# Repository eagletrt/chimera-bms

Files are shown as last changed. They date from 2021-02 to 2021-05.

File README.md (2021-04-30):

# Chimera high voltage BMS  - hardware

## Libraries
The projects don't include the libraries since they use the KiCAD official ones.
Set accordingly the variables `${KICAD_SYMBOL_DIR}` and `${KISYSMOD}` for 
`kicad-symbols` and `kicad-footprints` respectively.
**For `kicad-symbols` checkout the repo to `v5` for now to have the legacy ones.**

Don't rescue symbols!

## Repo structure
```
chimera-bms:hw-master
|-- docs/       # Docs and datasheets of common interest
|-- mainboard/  # MainBoard hardware project folder
|-- cellboard/  # CellBoard hardware project folder
```

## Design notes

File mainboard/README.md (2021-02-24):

# MAIN BOARD
Formula SAE - unitn

## Authors
Latest first:
- Filippo Volpe
- Gregor Gombac
- Jesus probably

## Project structure
```
mainboard
|-- MainBoard.pro           # Project file
|-- MainBoard.sch           # Schematic root
|-- MainBoard.kicad_pcb     # Board layout file
|-- MainBoard-cache.lib     # Local cache of symbols
|-- fp-info-cache           # Cache of footprints
|-- fp-lib-table            # List of footprint lib files
|-- sym-lib-table           # List of symbols lib files
|-- lib_sch/                # Local symbol library files
|-- modules/                # Local symbol library files
|   |-- MainBoard.pretty/   # Local footprint library files
|   |-- packages3d/         # 3D models
|-- outputs/
|   |-- MainBoard.stp       # Board 3D step file
|   |-- images/             # Board renders and such
|   |-- gerber/             # Gerbers outputs
|   |-- netlists/           # Netlists outputs
|-- docs/                   # Additional related documents and outputs
|   |-- Decoupling.txt      # List of decoupling capacitor needed
|   |-- bom/                # BOM folder
```

## Notes
The board file is from V2, it has not been updated

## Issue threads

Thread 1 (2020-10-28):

Add handcart sensing

Bonnee, 2020-10-28:
Automatically reconfigure the CAN-bus and initiate charging procedure when connected to the handcart.

volpx, 2021-02-28:
The pin for handcart detection has been added, the hardware side of the issue can be closed

Bonnee, 2021-02-28:
Perfect! How is the pin configured (pull-up or down)? Ideally it should be identical to the new Mainboard's one.

volpx, 2021-02-28:
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

volpx, 2021-02-28:
But it's not on the main connector as in fenice. the pinout is incompatible anyway.

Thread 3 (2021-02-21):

Add pin for hand cart detection

Bonnee, 2021-02-21:
Add input pin to check whether the battery is plugged into the car or is on the charging hand cart

Bonnee, 2021-02-21:
Duplicate of #1

Closed 2021-02-21.

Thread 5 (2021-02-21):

ADC doesn't work

Bonnee, 2021-02-21:
The external ADC of the old design doesn't work. I think it's better to replace it with the new Mainboard's design which seems to work.

volpx, 2021-02-24:
Old isoADC: LTC1865L
New from fenice: Si8900

volpx, 2021-02-27:
I'm working on changing the ADC but the Si8900 needs a UART+one output GPIO. So I moved some pins around to use empty pins and now the pinout is full:
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

volpx, 2021-02-27:
If we will need a MCU upgrade this would be a good time to.

Bonnee, 2021-02-27:
Wold going for the same MCU in a bigger package make sense? We don't really need more compute power or peripherals on this board.

volpx, 2021-02-28:
GG just wrote me suggesting to use the I2C version. Do we have one in the lab to try?

Bonnee, 2021-02-28:
We can do with the I2C version. I don't know if we have any of those chips in lab, but I don't think so.
What kind of memories do we have on the bus?

volpx, 2021-02-28:
two m24m02

Bonnee, 2021-02-28:
Never knew of their existance lol. You can remove one of those.

volpx, 2021-02-28:
Not a problem if they are there, we can just not populate the footprint. We go for the I2C adc then and call the issue closed once i push.

Closed 2021-02-28.

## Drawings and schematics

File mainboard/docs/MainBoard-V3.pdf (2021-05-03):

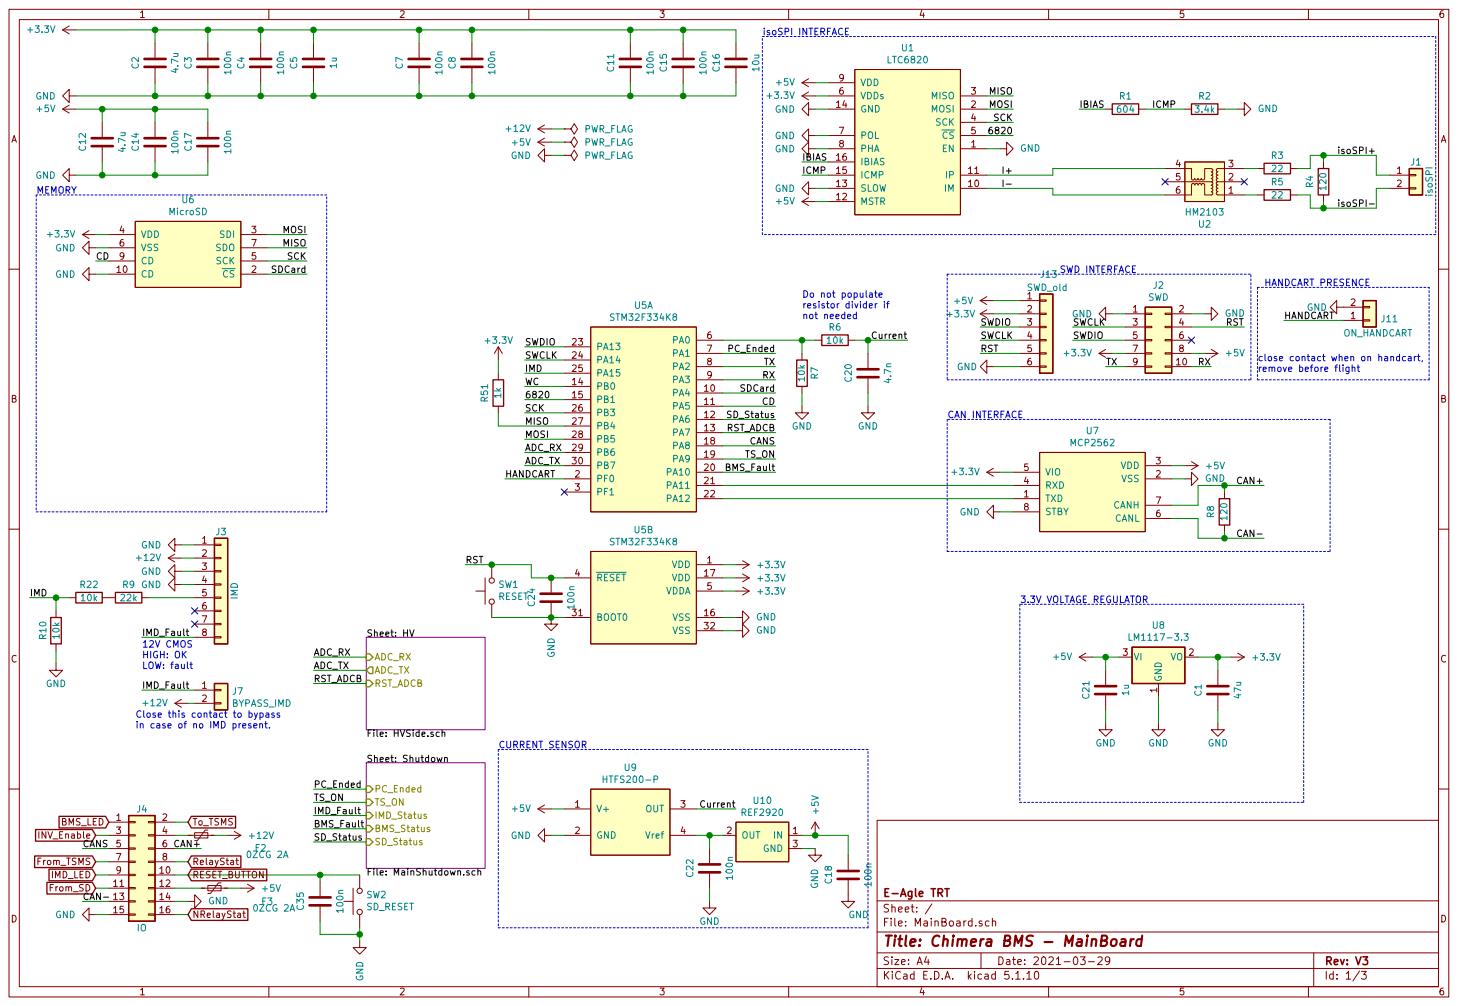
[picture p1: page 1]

close contact when on handcart, remove before flight HANDCART PRESENCE CAN INTERFACE Close this contact to bypass

resistor divider if not needed CURRENT SENSOR

in case of no IMD present.

Sheet: Shutdown File: MainShutdown.sch PC_Ended TS_ON

File: MainBoard.sch Sheet: / E-Agle TRT

GND
Id: 1/3 Title: Chimera BMS - MainBoard

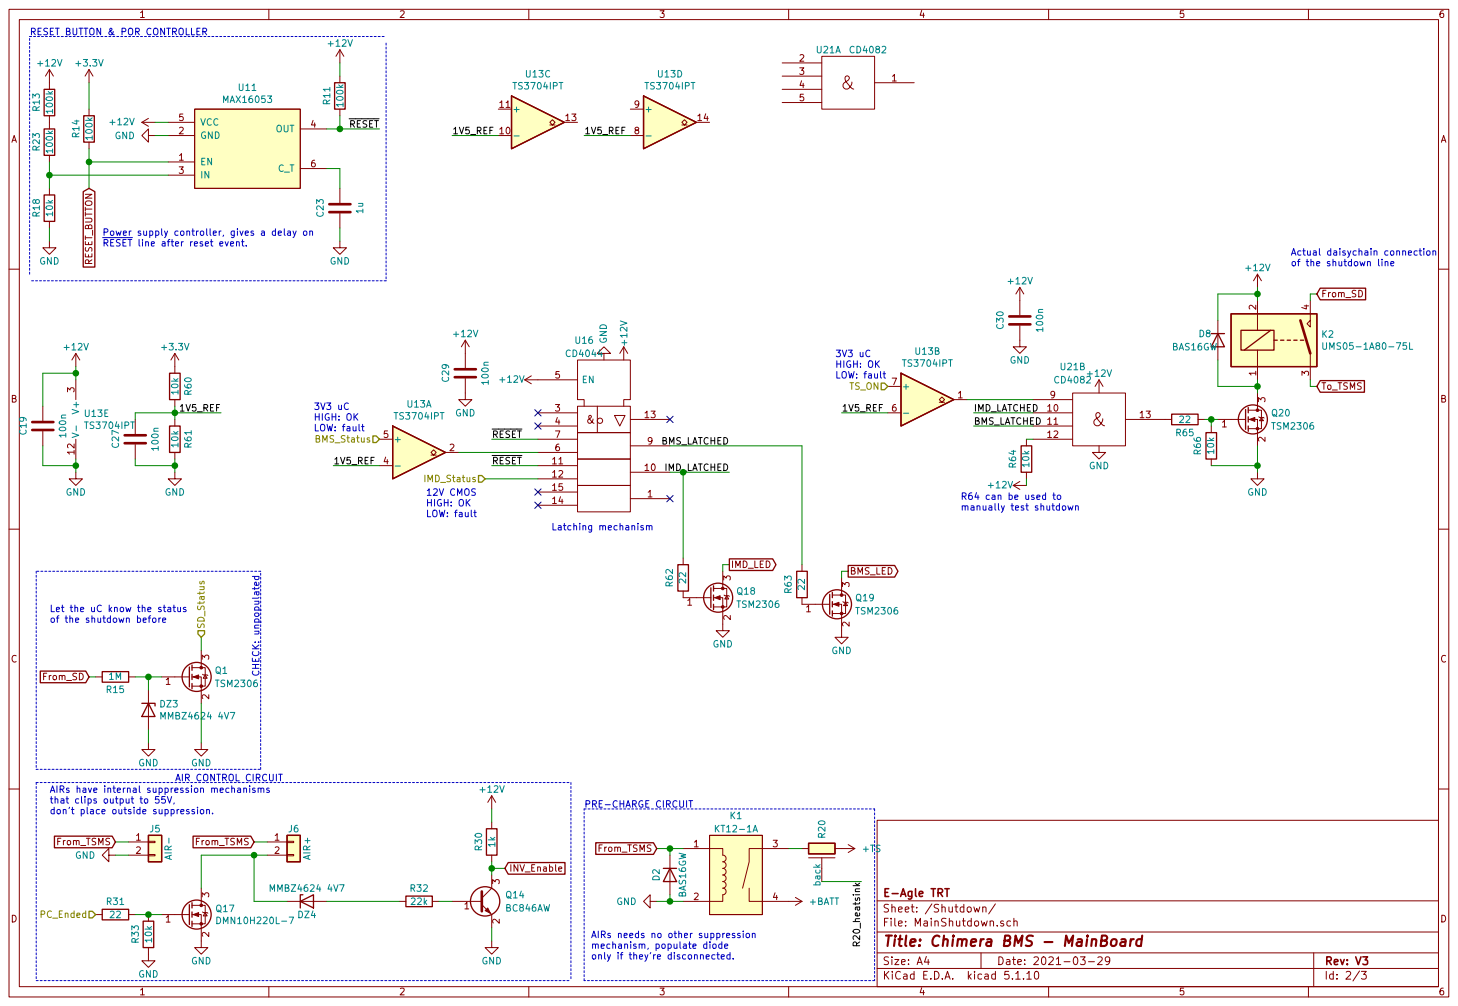
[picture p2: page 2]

RESET BUTTON & POR CONTROLLER

LOW: fault Power supply controller, gives a delay on RESET line after reset event. AIRs have internal suppression mechanisms

Actual daisychain connection of the shutdown line PRE-CHARGE CIRCUIT AIR CONTROL CIRCUIT
+12V GND

3 4 K2UMS05-1A80-75L GND
LOW: fault CHECK: unpopulated

Let the uC know the status of the shutdown before

R64 can be used to manually test shutdown

that clips output to 55V,
don't place outside suppression.

File: MainShutdown.sch Sheet: /Shutdown/ E-Agle TRT

Id: 2/3 Title: Chimera BMS - MainBoard

AIRs needs no other suppression
mechanism, populate diode
only if they're disconnected.

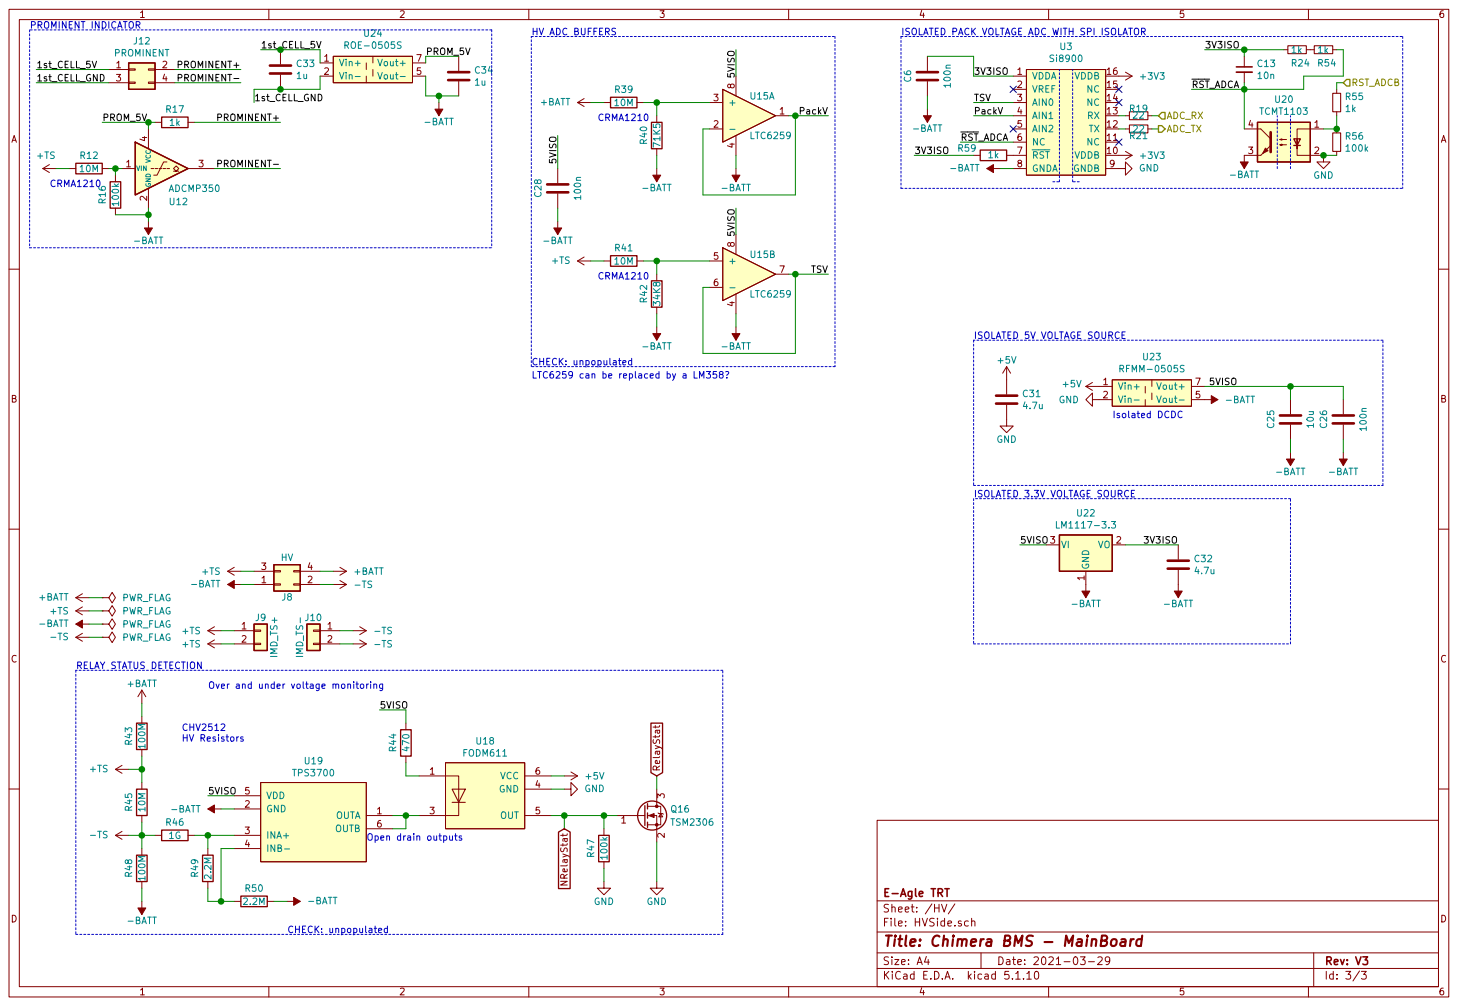
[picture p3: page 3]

ISOLATED PACK VOLTAGE ADC WITH SPI ISOLATOR

ISOLATED 5V VOLTAGE SOURCE CHECK: unpopulated

LTC6259 can be replaced by a LM358?

CHECK: unpopulated CHV2512 HV Resistors RELAY STATUS DETECTION Over and under voltage monitoring

Id: 3/3 Title: Chimera BMS - MainBoard

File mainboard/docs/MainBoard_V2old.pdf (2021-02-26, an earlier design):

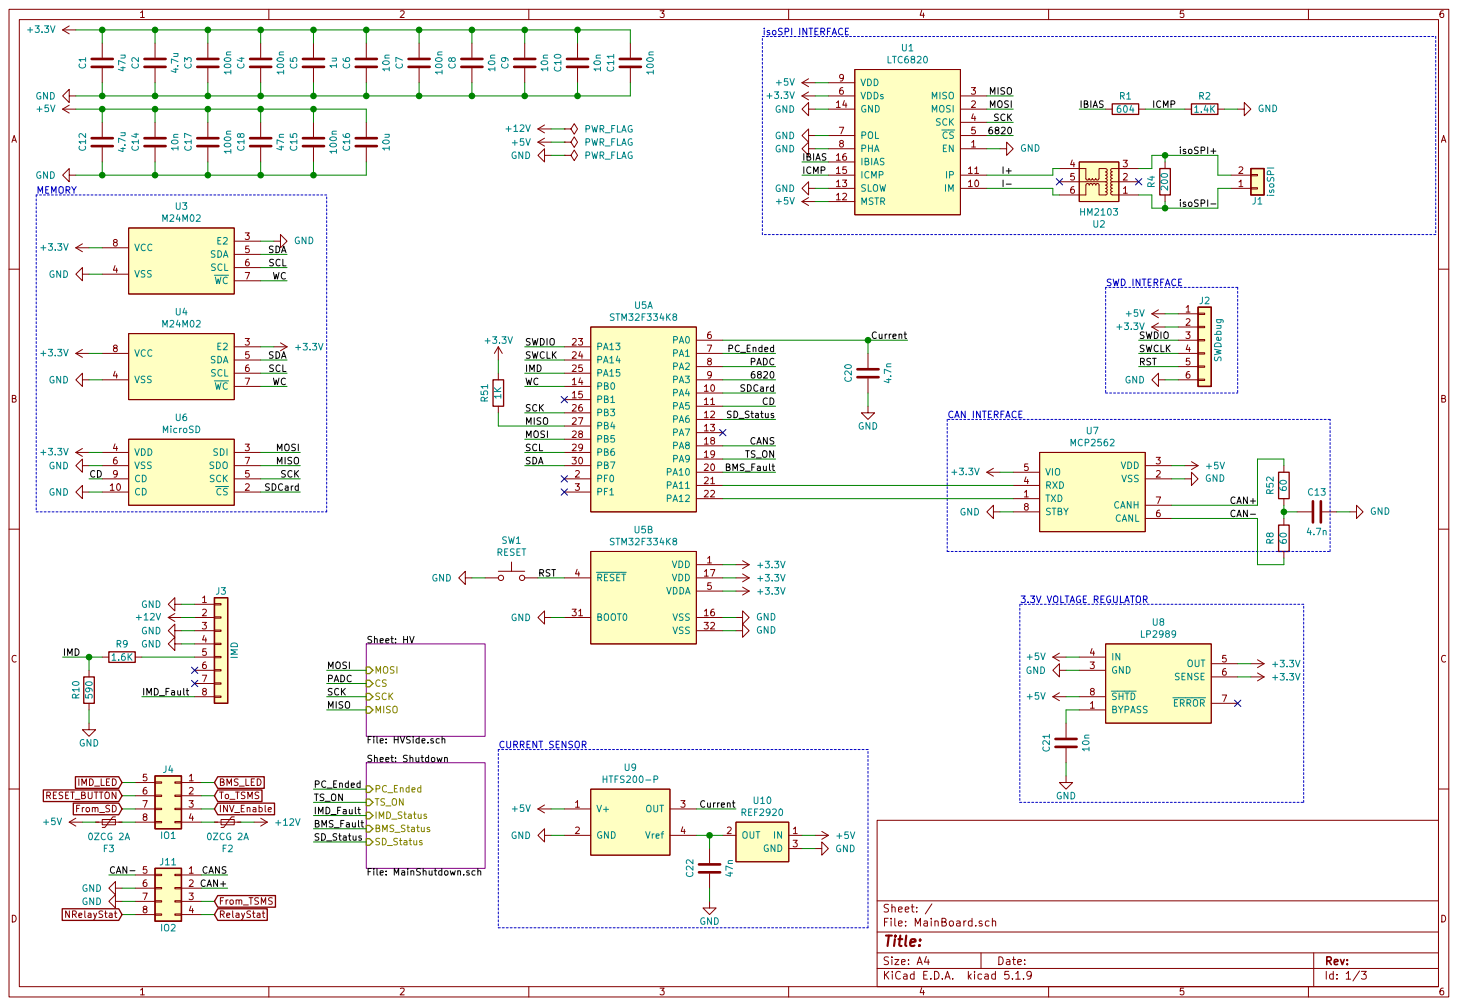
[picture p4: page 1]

SWD INTERFACE CURRENT SENSOR

File: HVSide.sch MOSI CS

Id: 1/3 Title: File: MainBoard.sch Sheet: / Sheet: Shutdown File: MainShutdown.sch PC_Ended TS_ON

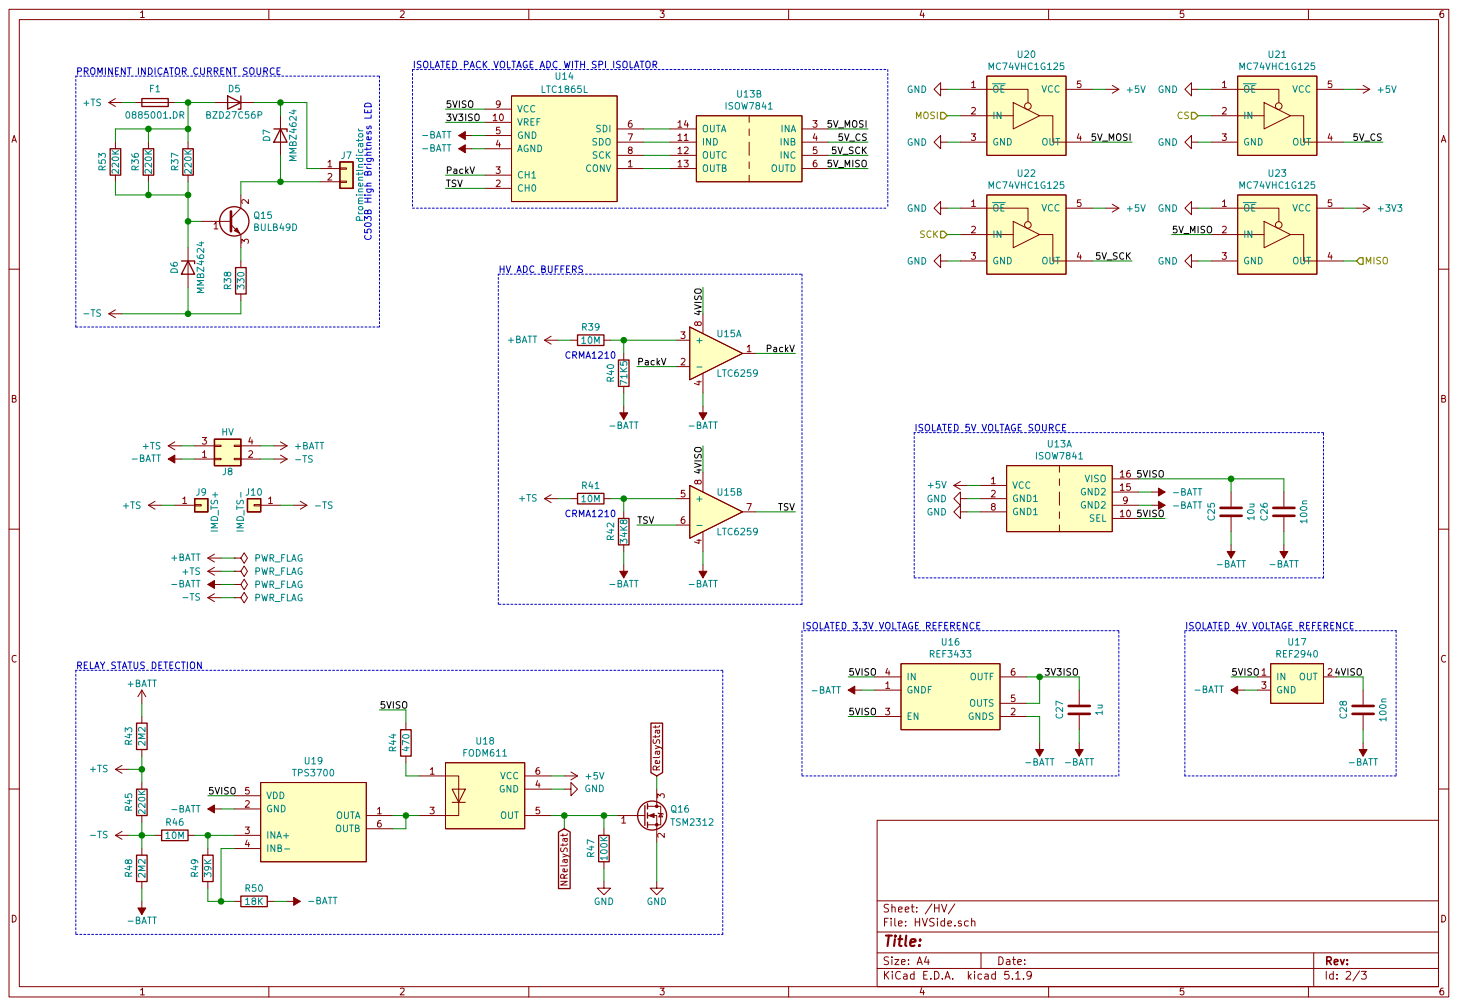
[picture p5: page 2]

ISOLATED PACK VOLTAGE ADC WITH SPI ISOLATOR

Id: 2/3 Title: File: HVSide.sch Sheet: /HV/

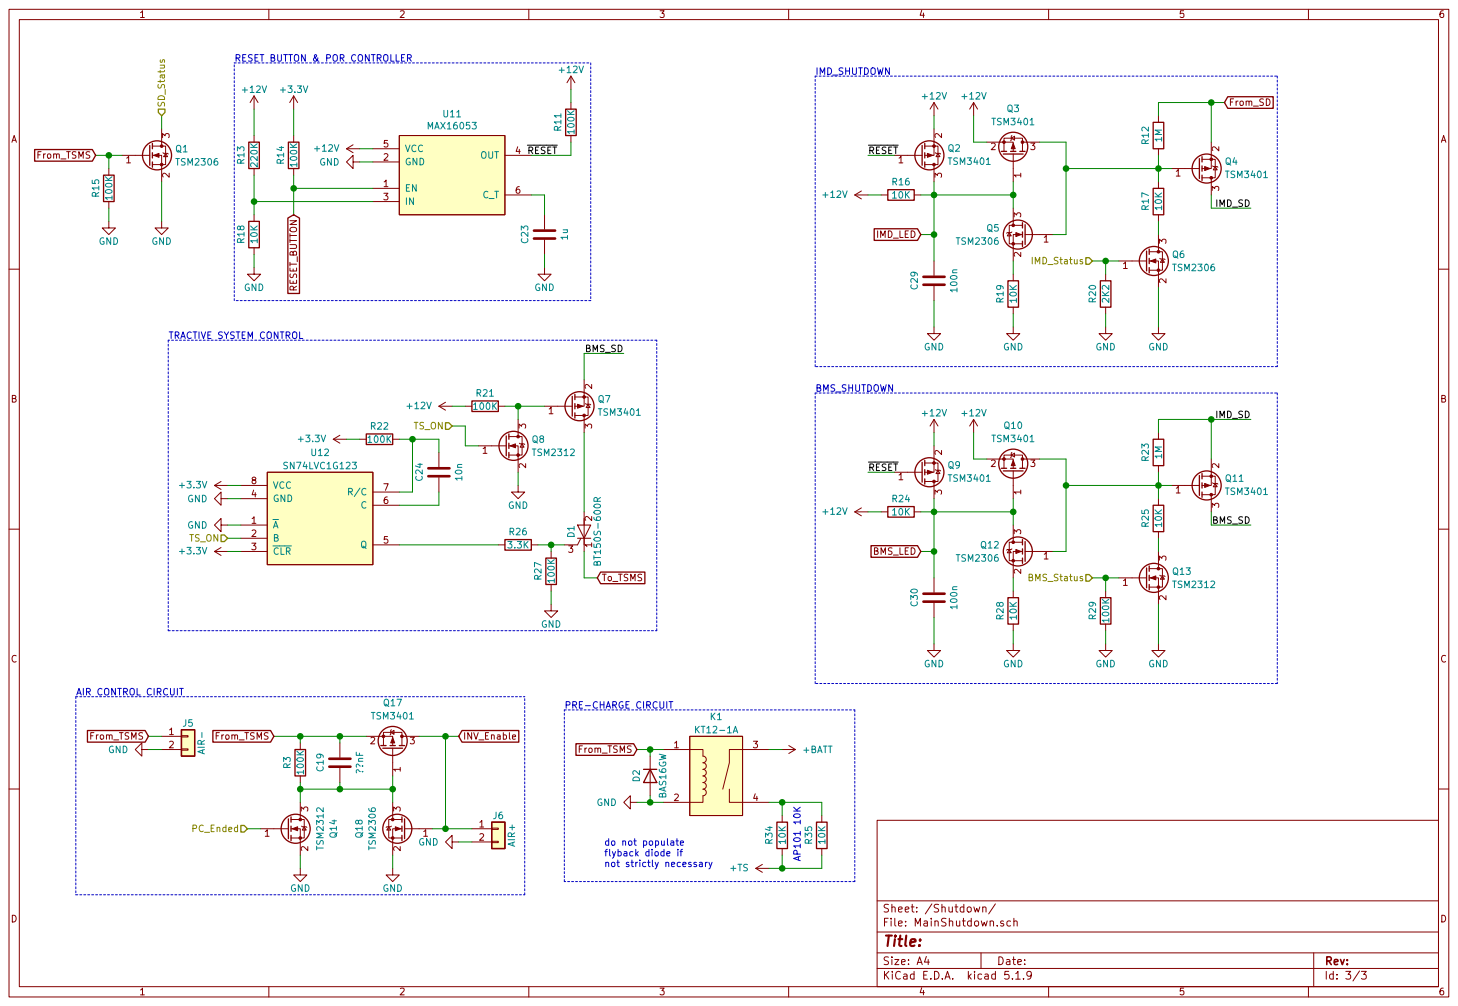
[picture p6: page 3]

TRACTIVE SYSTEM CONTROL RESET BUTTON & POR CONTROLLER

PRE-CHARGE CIRCUIT AIR CONTROL CIRCUIT

Id: 3/3 Title: File: MainShutdown.sch Sheet: /Shutdown/ +BATT

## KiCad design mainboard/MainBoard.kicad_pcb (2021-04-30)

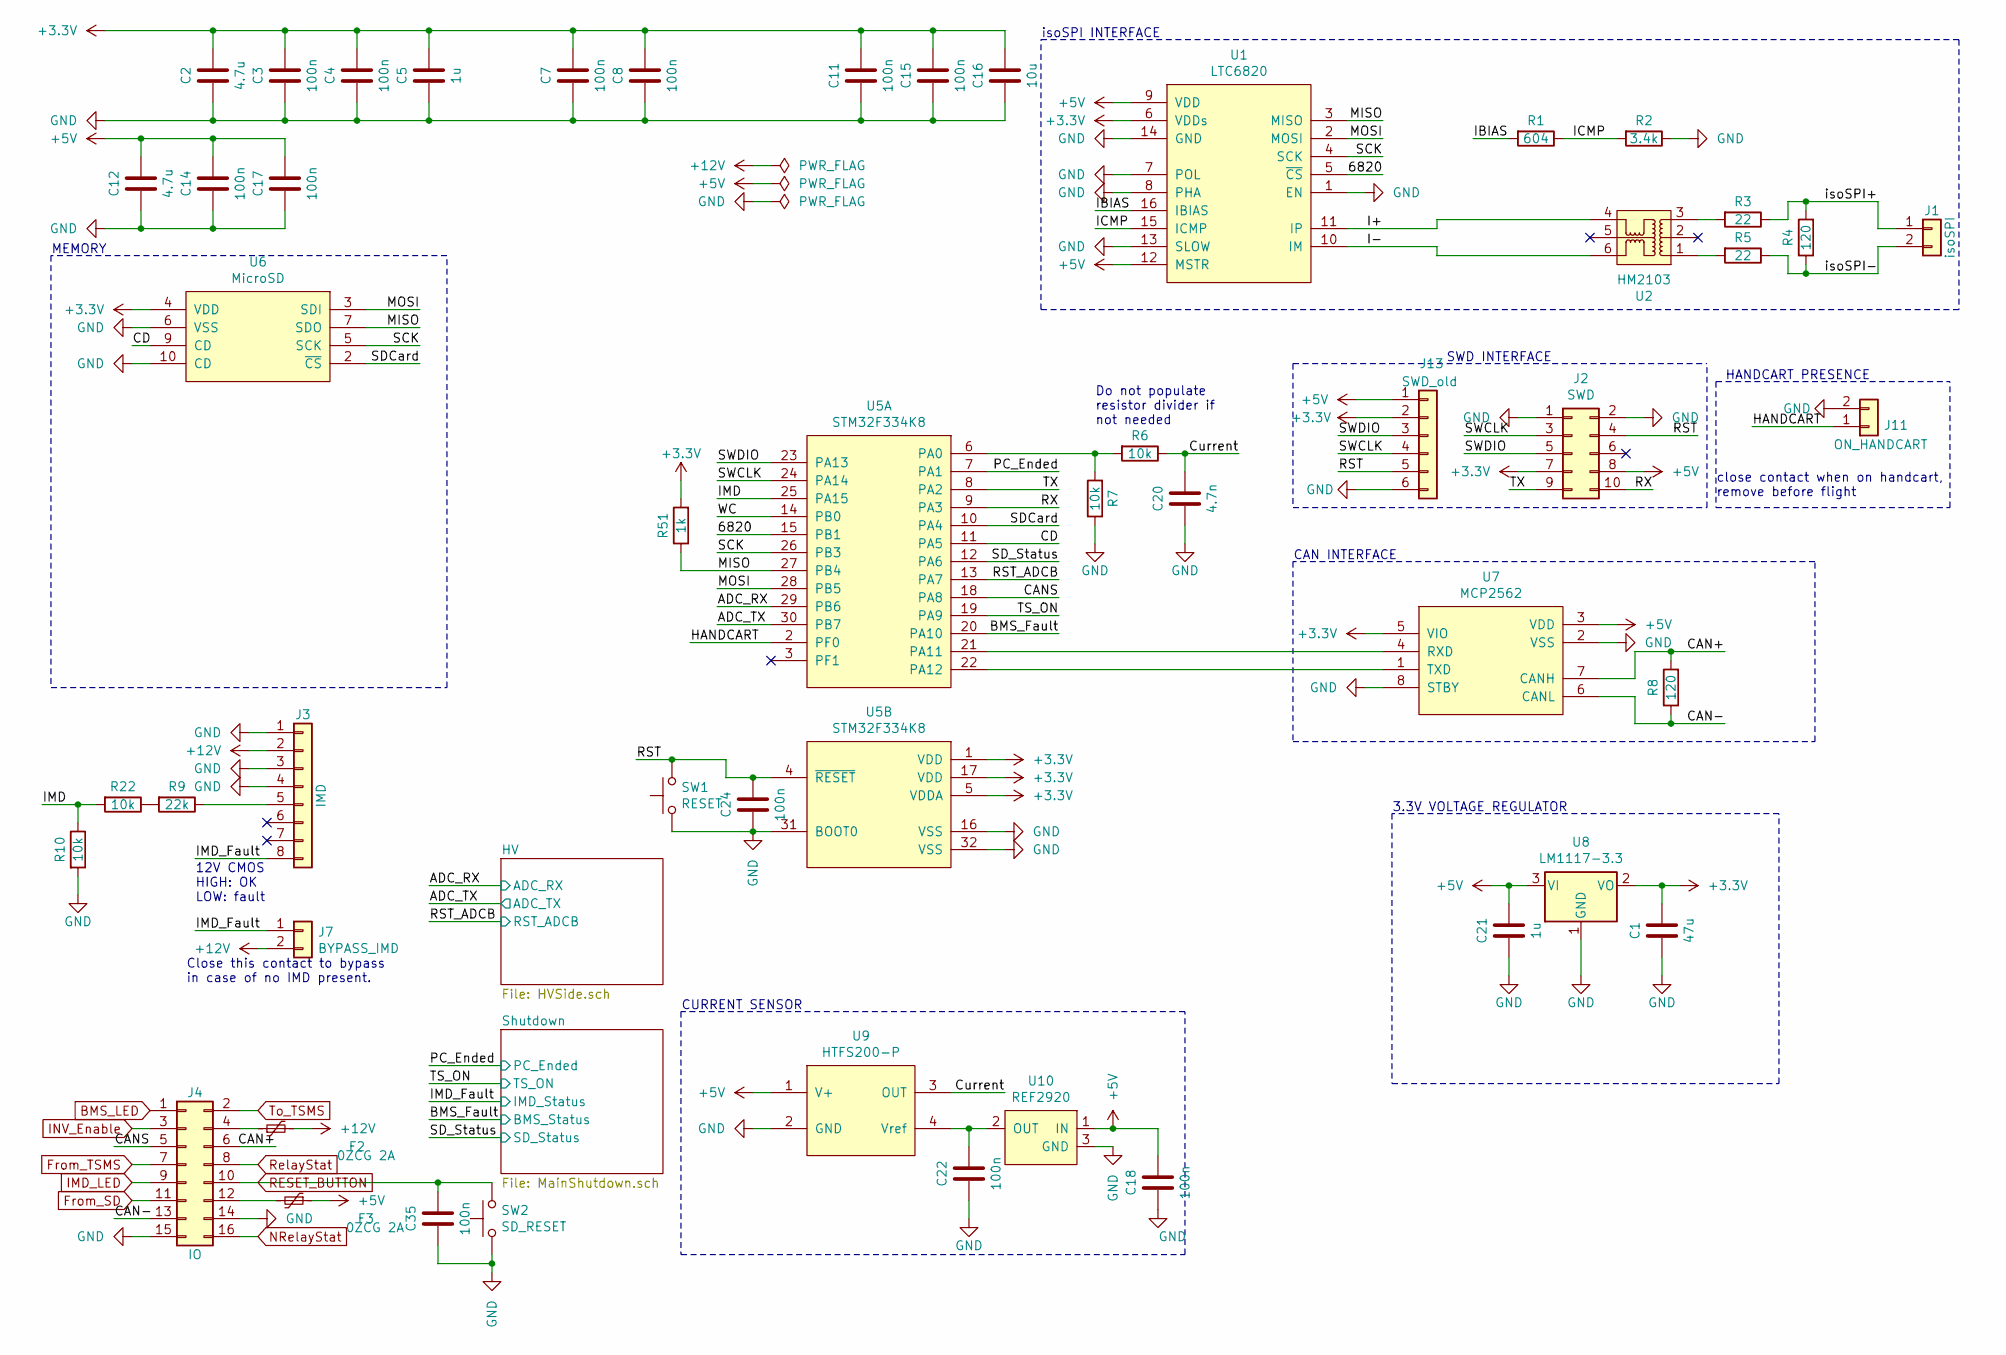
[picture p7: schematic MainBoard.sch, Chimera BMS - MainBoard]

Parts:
C1: 47u; C_1206_3216Metric
C2, C12: 4.7u; C_0805_2012Metric
C3, C4, C7, C8, C11, C14, C15, C17, C18, C22, C24, C35: 100n; C_0603_1608Metric
C5, C21: 1u; C_0805_2012Metric
C16: 10u; C_0805_2012Metric
C20: 4.7n; C_0603_1608Metric
F2, F3: 0ZCG 2A; Fuse_1812_4532Metric
J1: isoSPI; Molex_Micro-Fit_3.0_43650-0215_1x02_P3.00mm_Vertical
J2: SWD; PinHeader_2x05_P2.54mm_Vertical
J3: IMD; PinHeader_1x08_P3mm_Vertical
J4: IO; Molex_Micro-Fit_3.0_43045-1612_2x08_P3.00mm_Vertical
J7: BYPASS_IMD; PinHeader_1x02_P2.54mm_Vertical
J11: ON_HANDCART; PinHeader_1x02_P2.54mm_Vertical
J13: SWD_old; PinHeader_1x06_P2.54mm_Vertical
R1: 604; R_0805_2012Metric
R2: 3.4k; R_0805_2012Metric
R3, R5: 22; R_0805_2012Metric
R4, R8: 120; R_0805_2012Metric
R6, R7, R10, R22: 10k; R_0805_2012Metric
R9: 22k; R_0805_2012Metric
R51: 1k; R_0805_2012Metric
SW1: RESET; SW_SPST_FSMSM
SW2: SD_RESET; SW_SPST_FSMSM
U1: LTC6820; MSOP-16
U2: HM2103
U5: STM32F334K8; LQFP-32_7x7mm_P0.8mm
U6: MicroSD; Molex_MicroSD_PushPull
U7: MCP2562; SOIC-8_3.9x4.9mm_P1.27mm
U8: LM1117-3.3; SOT-223-3_TabPin2
U9: HTFS200-P; HTFS 200-P
U10: REF2920; SOT-23

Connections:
+5V: C12.1, C14.1, C17.1, C18.1, C21.1, F3.1, J2.8, J13.1, U1.9 (VDD), U1.12 (MSTR), U7.3 (VDD), U8.3 (VI), U9.1 (V+), U10.1 (IN); also elsewhere on the board
+12V: F2.2, J3.2, J7.2; also elsewhere on the board
/6820: U1.5 (~CS), U5.15 (PB1)
/ADC_RX: U5.29 (PB6); also elsewhere on the board
/ADC_TX: U5.30 (PB7); also elsewhere on the board
/BMS_Fault: U5.20 (PA10); also elsewhere on the board
/CAN+: J4.6, R8.2, U7.7 (CANH)
/CAN-: J4.13, R8.1, U7.6 (CANL)
/CANS: J4.5, U5.18 (PA8)
/CD: U5.11 (PA5), U6.9 (CD)
/Current: C20.1, R6.1, U9.3 (OUT)
/HANDCART: J11.1, U5.2 (PF0)
/I+: U1.11 (IP), U2.4
/I-: U1.10 (IM), U2.6
/IBIAS: R1.2, U1.16 (IBIAS)
/ICMP: R1.1, R2.2, U1.15 (ICMP)
/IMD: R10.1, R22.2, U5.25 (PA15)
/IMD_Fault: J3.8, J7.1; also elsewhere on the board
/MISO: R51.1, U1.3 (MISO), U5.27 (PB4), U6.7 (SDO)
/MOSI: U1.2 (MOSI), U5.28 (PB5), U6.3 (SDI)
/PC_Ended: U5.7 (PA1); also elsewhere on the board
/RST: C24.1, J2.4, J13.5, SW1.2, U5.4 (~RESET)
/RST_ADCB: U5.13 (PA7); also elsewhere on the board
/RX: J2.10, U5.9 (PA3)
/SCK: U1.4 (SCK), U5.26 (PB3), U6.5 (SCK)
/SDCard: U5.10 (PA4), U6.2 (~CS)
/SD_Status: U5.12 (PA6); also elsewhere on the board
/SWCLK: J2.3, J13.4, U5.24 (PA14)
/SWDIO: J2.5, J13.3, U5.23 (PA13)
/TS_ON: U5.19 (PA9); also elsewhere on the board
/TX: J2.9, U5.8 (PA2)
/WC: U5.14 (PB0)
/isoSPI+: J1.1, R3.1, R4.2
/isoSPI-: J1.2, R4.1, R5.1
BMS_LED: J4.1; also elsewhere on the board
From_SD: J4.11; also elsewhere on the board
From_TSMS: J4.7; also elsewhere on the board
GND: C1.2, C2.2, C3.2, C4.2, C5.2, C7.2, C8.2, C11.2, C12.2, C14.2, C15.2, C16.2, C17.2, C18.2, C20.2, C21.2, C22.2, C24.2, C35.2, J2.1, J2.2, J3.1, J3.3, J3.4, J4.14, J4.15, J11.2, J13.6, R2.1, R7.1, R10.2, SW1.1, SW2.1, U1.1 (EN), U1.7 (POL), U1.8 (PHA), U1.13 (SLOW), U1.14 (GND), U5.16 (VSS), U5.31 (BOOT0), U5.32 (VSS), U6.6 (VSS), U6.10 (CD), U7.2 (VSS), U7.8 (STBY), U8.1 (GND), U9.2 (GND), U10.3 (GND); also elsewhere on the board
IMD_LED: J4.9; also elsewhere on the board
INV_Enable: J4.3; also elsewhere on the board
NRelayStat: J4.16; also elsewhere on the board
unnamed: C22.1, U9.4 (Vref), U10.2 (OUT)
unnamed: F2.1, J4.4
unnamed: F3.2, J4.12
unnamed: J3.5, R9.1
unnamed: R3.2, U2.3
unnamed: R5.2, U2.1
unnamed: R6.2, R7.2, U5.6 (PA0)
unnamed: R9.2, R22.1
unnamed: U5.21 (PA11), U7.4 (RXD)
unnamed: U5.22 (PA12), U7.1 (TXD)
RESET_BUTTON: C35.1, J4.10, SW2.2; also elsewhere on the board
RelayStat: J4.8; also elsewhere on the board
To_TSMS: J4.2; also elsewhere on the board

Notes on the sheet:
MEMORY
isoSPI INTERFACE
CAN INTERFACE
3.3V VOLTAGE REGULATOR
SWD INTERFACE
Do not populate resistor divider if not needed
CURRENT SENSOR
HANDCART PRESENCE
close contact when on handcart, remove before flight
12V CMOS HIGH: OK LOW: fault
Close this contact to bypass in case of no IMD present.

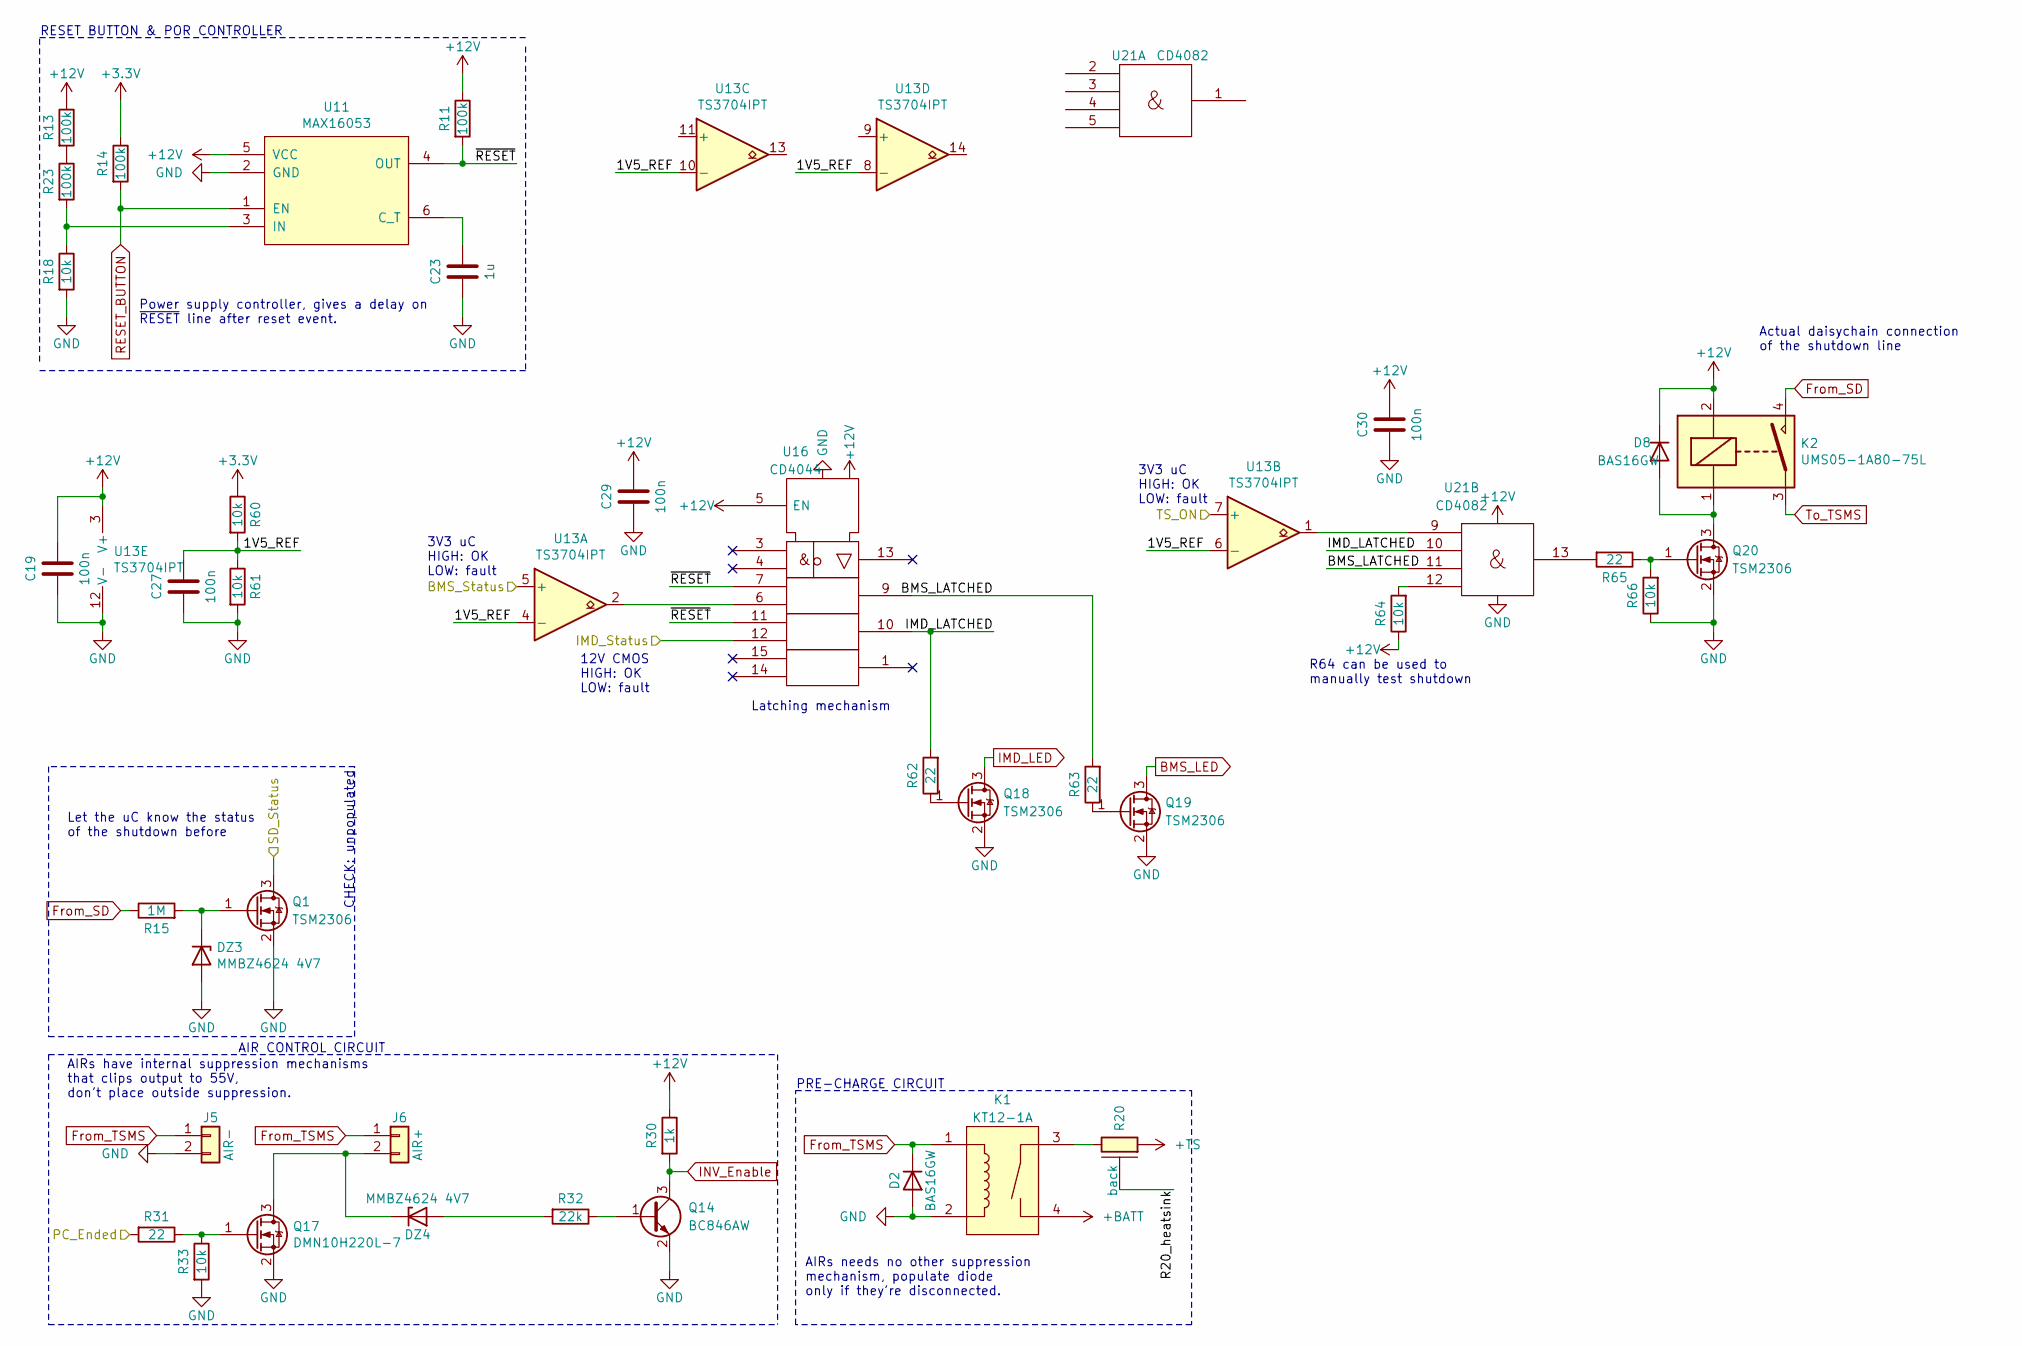
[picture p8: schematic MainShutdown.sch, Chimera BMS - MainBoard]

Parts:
C19, C27, C29, C30: 100n; C_0603_1608Metric
C23: 1u; C_0805_2012Metric
D2, D8: BAS16GW; D_SOD-123
DZ3, DZ4: MMBZ4624 4V7; D_SOT-23_ANK
J5: AIR-; Molex_Micro-Fit_3.0_43650-0215_1x02_P3.00mm_Vertical
J6: AIR+; Molex_Micro-Fit_3.0_43650-0215_1x02_P3.00mm_Vertical
K1: KT12-1A; KT_THT
K2: UMS05-1A80-75L; G6DN-1A_DC12
Q1, Q18, Q19, Q20: TSM2306; SOT-23
Q14: BC846AW; SOT-23
Q17: DMN10H220L-7; SOT-23
R11, R13, R14, R23: 100k; R_0805_2012Metric
R15: 1M; R_0805_2012Metric
R18, R33, R60, R61, R64, R66: 10k; R_0805_2012Metric
R20: PWR163S-25-1002J 10k; pwr163
R30: 1k; R_0805_2012Metric
R31, R62, R63, R65: 22; R_0805_2012Metric
R32: 22k; R_0805_2012Metric
U11: MAX16053; SOT-23-6
U13: TS3704IPT; TSSOP-14_4.4x5mm_P0.65mm
U16: CD4044; TSSOP-16_4.4x5mm_P0.65mm
U21: CD4082; TSSOP-14_4.4x5mm_P0.65mm

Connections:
+12V: C19.1, C29.1, C30.1, D8.1 (K), K2.2, R11.1, R13.1, R30.1, R64.1, U11.5 (VCC), U13.3 (V+), U16.5 (EN), U16.16 (Vdd), U21.14 (Vdd); also elsewhere on the board
+BATT: K1.4; also elsewhere on the board
+TS: R20.2; also elsewhere on the board
/BMS_Fault: U13.5 (+); also elsewhere on the board
/IMD_Fault: U16.12; also elsewhere on the board
/PC_Ended: R31.2; also elsewhere on the board
/SD_Status: Q1.3 (D); also elsewhere on the board
/Shutdown/1V5_REF: C27.1, R60.2, R61.1, U13.4 (-), U13.6 (-), U13.8 (-), U13.10 (-)
/Shutdown/BMS_LATCHED: R63.2, U16.9, U21.11
/Shutdown/IMD_LATCHED: R62.2, U16.10, U21.10
/Shutdown/R20_heatsink: R20.3 (back)
/Shutdown/~RESET: R11.2, U11.4 (OUT), U16.7, U16.11
/TS_ON: U13.7 (+); also elsewhere on the board
BMS_LED: Q19.3 (D); also elsewhere on the board
From_SD: K2.4, R15.1; also elsewhere on the board
From_TSMS: D2.1 (K), J5.1, J6.1, K1.1; also elsewhere on the board
GND: C19.2, C23.2, C27.2, C29.2, C30.2, D2.2 (A), DZ3.2 (A), J5.2, K1.2, Q1.2 (S), Q14.2 (E), Q17.2 (S), Q18.2 (S), Q19.2 (S), Q20.2 (S), R18.2, R33.2, R61.2, R66.1, U11.2 (GND), U13.12 (V-), U16.8 (Vss), U21.7 (Vss); also elsewhere on the board
IMD_LED: Q18.3 (D); also elsewhere on the board
INV_Enable: Q14.3 (C), R30.2; also elsewhere on the board
unnamed: C23.1, U11.6 (C_T)
unnamed: D8.2 (A), K2.1, Q20.3 (D)
unnamed: DZ3.1 (K), Q1.1 (G), R15.2
unnamed: DZ4.1 (K), J6.2, Q17.3 (D)
unnamed: DZ4.2 (A), R32.2
unnamed: K1.3, R20.1
unnamed: Q14.1 (B), R32.1
unnamed: Q17.1 (G), R31.1, R33.1
unnamed: Q18.1 (G), R62.1
unnamed: Q19.1 (G), R63.1
unnamed: Q20.1 (G), R65.1, R66.2
unnamed: R13.2, R23.1
unnamed: R18.1, R23.2, U11.3 (IN)
unnamed: R64.2, U21.12
unnamed: R65.2, U21.13
unnamed: U13.1, U21.9
unnamed: U13.2, U16.6
RESET_BUTTON: R14.2, U11.1 (EN); also elsewhere on the board
To_TSMS: K2.3; also elsewhere on the board

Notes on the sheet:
PRE-CHARGE CIRCUIT
AIR CONTROL CIRCUIT
RESET BUTTON & POR CONTROLLER
12V CMOS HIGH: OK LOW: fault
Power supply controller, gives a delay on ~RESET~ line after reset event.
3V3 uC HIGH: OK LOW: fault
Latching mechanism
Let the uC know the status of the shutdown before
Actual daisychain connection of the shutdown line
R64 can be used to manually test shutdown
CHECK: unpopulated
AIRs needs no other suppression mechanism, populate diode only if they're disconnected.
AIRs have internal suppression mechanisms that clips output to 55V, don't place outside suppression.

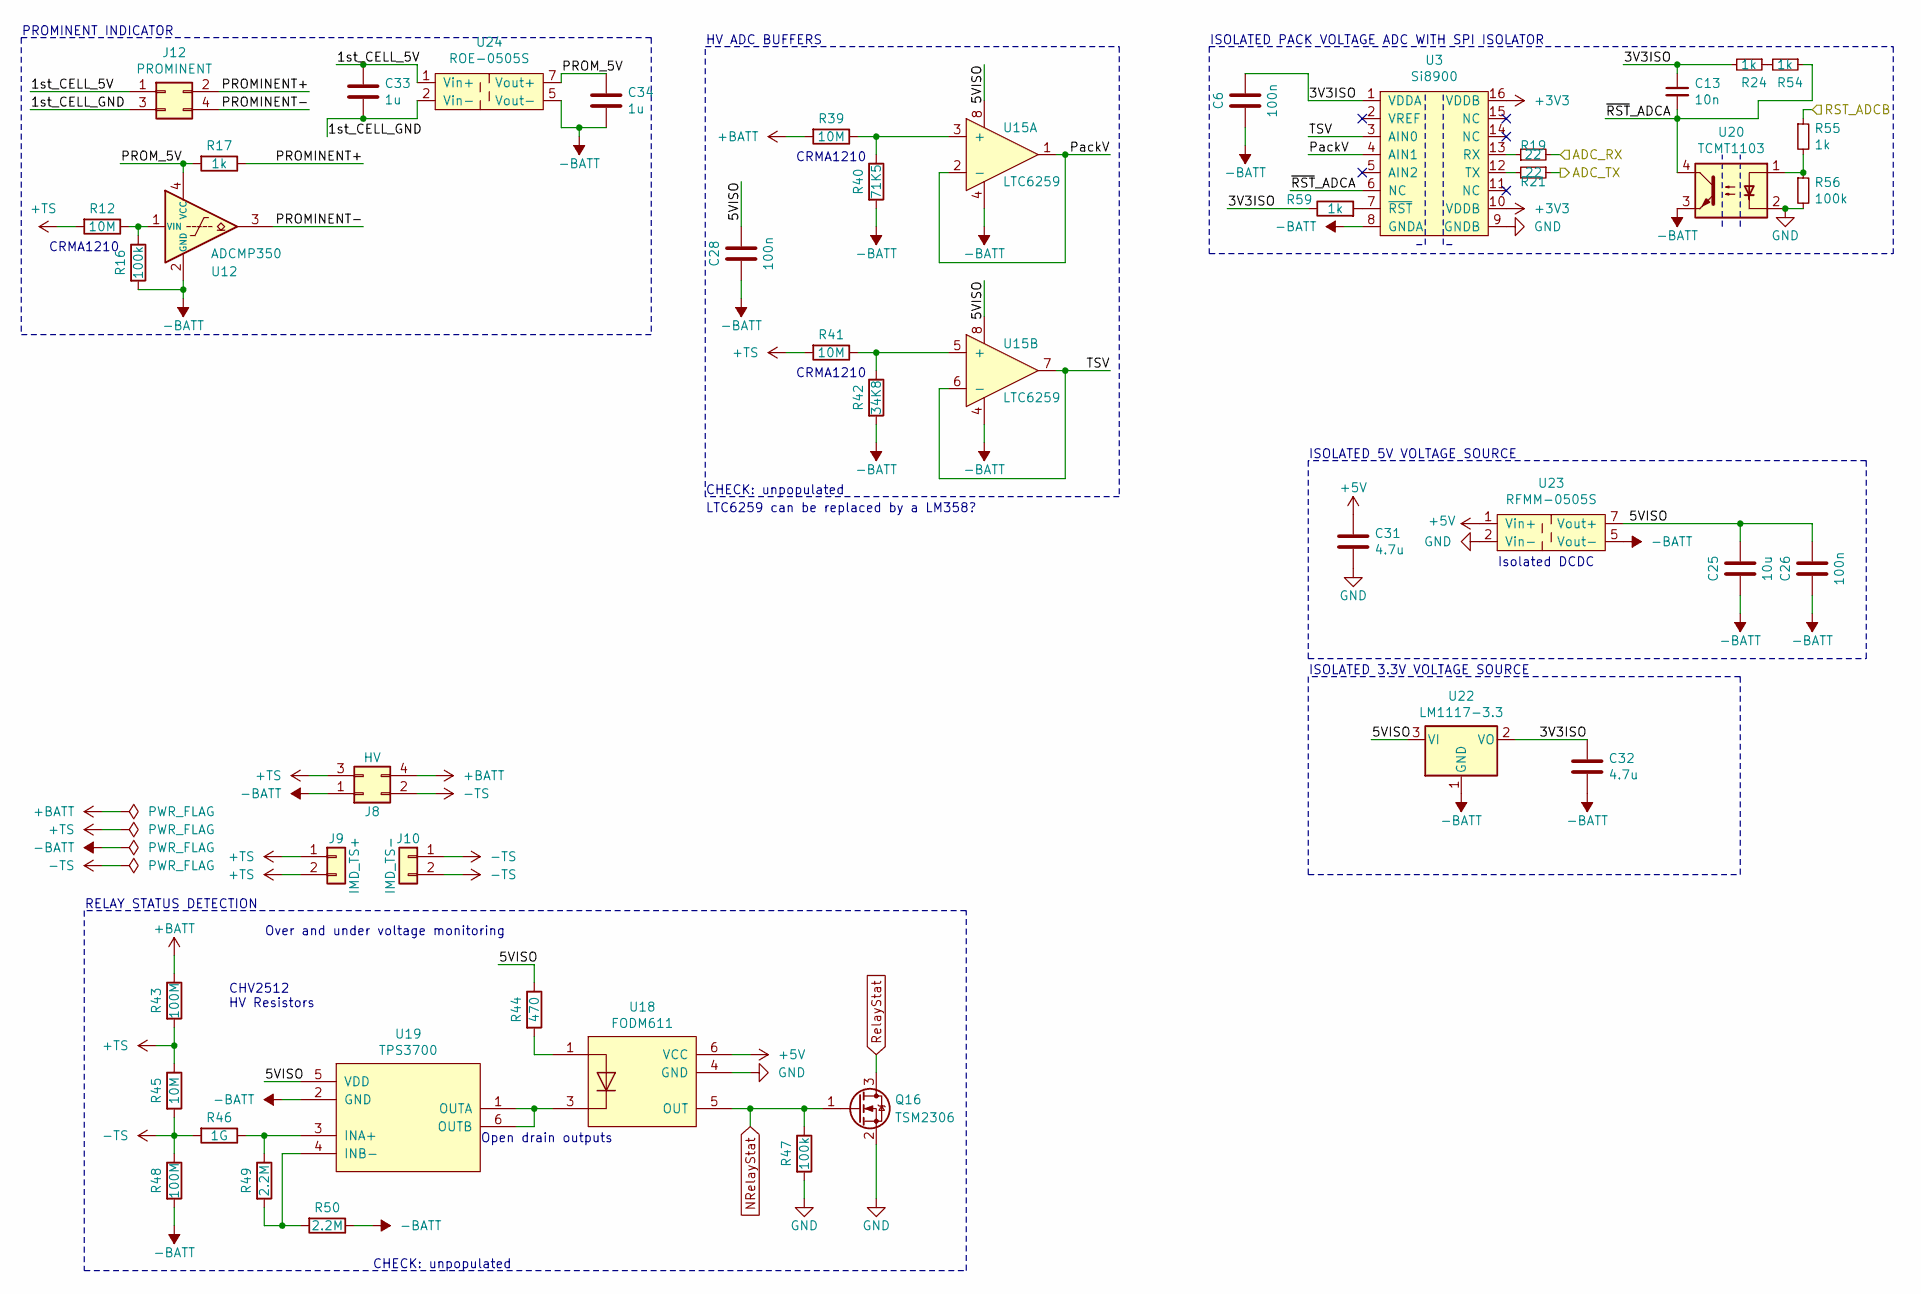
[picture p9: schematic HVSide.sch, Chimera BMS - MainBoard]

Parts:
C6, C26, C28: 100n; C_0603_1608Metric
C13: 10n; C_0603_1608Metric
C25: 10u; C_0805_2012Metric
C31, C32: 4.7u; C_0805_2012Metric
C33, C34: 1u; C_0805_2012Metric
J8: HV; Molex_Mega-Fit_76829-0104_2x02_P5.70mm_Vertical
J9: IMD_TS+; PinHeader_1x02_P3mm_Vertical
J10: IMD_TS-; PinHeader_1x02_P3mm_Vertical
J12: PROMINENT; Molex_Micro-Fit_3.0_43045-0412_2x02_P3.00mm_Vertical
Q16: TSM2306; SOT-23
R12, R39, R41: 10M; R_1210_3225Metric
R16, R47, R56: 100k; R_0805_2012Metric
R17, R24, R54, R55, R59: 1k; R_0805_2012Metric
R19, R21: 22; R_0805_2012Metric
R40: 71K5; R_0805_2012Metric
R42: 34K8; R_0805_2012Metric
R43, R48: 100M; R_2512_6332Metric
R44: 470; R_0805_2012Metric
R45: 10M; R_2512_6332Metric
R46: 1G; R_2512_6332Metric
R49, R50: 2.2M; R_2512_6332Metric
U3: Si8900; SOIC-16
U12: ADCMP350; Analog_KS-4
U15: LTC6259; MSOP-8_and_TSOT-23-8
U18: FODM611
U19: TPS3700; SOT-23-6
U20: TCMT1103; SOP-4_4.4x2.6mm_P1.27mm
U22: LM1117-3.3; SOT-223-3_TabPin2
U23: RFMM-0505S
U24: ROE-0505S

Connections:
+5V: C31.1, U18.6 (VCC), U23.1 (Vin+); also elsewhere on the board
+BATT: J8.4, R39.2, R43.1; also elsewhere on the board
+TS: J8.3, J9.1, J9.2, R12.2, R41.2, R43.2, R45.1; also elsewhere on the board
-BATT: C6.2, C25.2, C26.2, C28.2, C32.2, C34.2, J8.1, R16.2, R40.2, R42.2, R48.2, R50.1, U3.8 (GNDA), U12.2 (GND), U15.4, U19.2 (GND), U20.3, U22.1 (GND), U23.5 (Vout-), U24.5 (Vout-)
-TS: J8.2, J10.1, J10.2, R45.2, R46.2, R48.1
/ADC_RX: R19.2; also elsewhere on the board
/ADC_TX: R21.1; also elsewhere on the board
/HV/1st_CELL_5V: C33.1, J12.1, U24.1 (Vin+)
/HV/1st_CELL_GND: C33.2, J12.3, U24.2 (Vin-)
/HV/3V3ISO: C6.1, C13.1, C32.1, R24.2, R59.1, U3.1 (VDDA), U22.2 (VO)
/HV/5VISO: C25.1, C26.1, C28.1, R44.1, U15.8, U19.5 (VDD), U22.3 (VI), U23.7 (Vout+)
/HV/PROMINENT+: J12.2, R17.1
/HV/PROMINENT-: J12.4, U12.3
/HV/PROM_5V: C34.1, R17.2, U12.4 (VCC), U24.7 (Vout+)
/HV/PackV: U3.4 (AIN1), U15.1, U15.2 (-)
/HV/TSV: U3.3 (AIN0), U15.6 (-), U15.7
/HV/~RST~_ADCA: C13.2, R54.1, U3.6 (NC), U20.4
/RST_ADCB: R55.1; also elsewhere on the board
GND: C31.2, Q16.2 (S), R47.2, R56.2, U3.9 (GNDB), U18.4 (GND), U20.2, U23.2 (Vin-); also elsewhere on the board
NRelayStat: Q16.1 (G), R47.1, U18.5 (OUT); also elsewhere on the board
unnamed: R12.1, R16.1, U12.1 (VIN)
unnamed: R19.1, U3.13 (RX)
unnamed: R21.2, U3.12 (TX)
unnamed: R24.1, R54.2
unnamed: R39.1, R40.1, U15.3 (+)
unnamed: R41.1, R42.1, U15.5 (+)
unnamed: R44.2, U18.1
unnamed: R46.1, R49.1, U19.3 (INA+)
unnamed: R49.2, R50.2, U19.4 (INB-)
unnamed: R55.2, R56.1, U20.1
unnamed: R59.2, U3.7 (~RST)
unnamed: U18.3, U19.1 (OUTA), U19.6 (OUTB)
RelayStat: Q16.3 (D); also elsewhere on the board

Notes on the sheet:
CRMA1210
CHV2512 HV Resistors
RELAY STATUS DETECTION
ISOLATED 5V VOLTAGE SOURCE
ISOLATED 3.3V VOLTAGE SOURCE
HV ADC BUFFERS
ISOLATED PACK VOLTAGE ADC WITH SPI ISOLATOR
Open drain outputs
Over and under voltage monitoring
CHECK: unpopulated
Isolated DCDC
PROMINENT INDICATOR
LTC6259 can be replaced by a LM358?

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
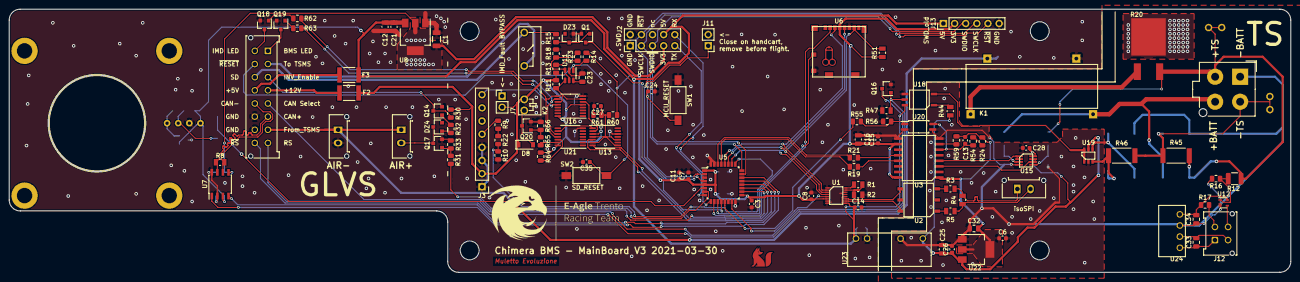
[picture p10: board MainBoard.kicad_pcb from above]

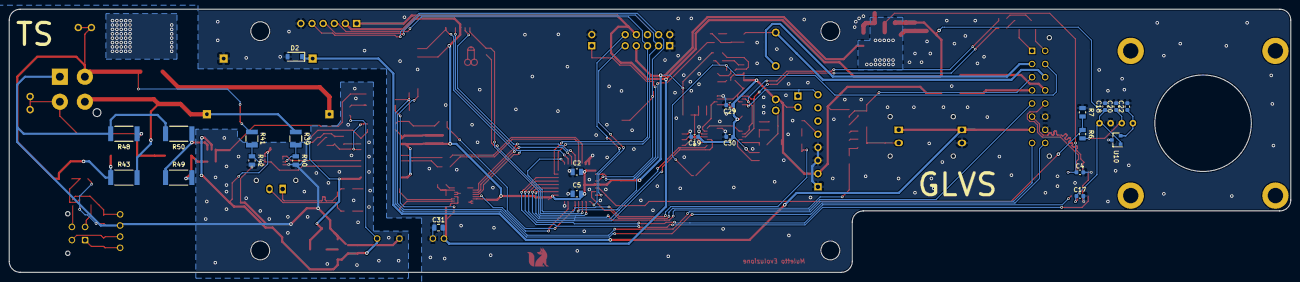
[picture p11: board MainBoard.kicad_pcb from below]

Board: 2 copper layers, 292.2 x 60.0 mm, 136 parts (23 on the bottom side), 101 nets.

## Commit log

2021-02-24 import of v1
    Imported the project from GG, this is the version of the last print
    [HVSide.sch, MainBoard.kicad_pcb, MainBoard.sch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]
2021-02-26 added V2 schematic
2021-02-27 change isoadc in schematic and documents
    [HVSide.sch, MainBoard.sch]
2021-02-28 i2c isoadc 8901
    [HVSide.sch, MainBoard.sch, MainShutdown.sch]
2021-02-28 adding handcart detection
    [HVSide.sch, MainBoard.sch]
2021-03-15 Shutdown logic to use gates, changed mosfets
    Shutdown ported from new car, mosfets changed to higher VGS max
    [HVSide.sch, MainBoard.kicad_pcb, MainBoard.sch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]
2021-03-27 ported shutdown from new car
    [MainShutdown.sch]
2021-03-27 new SWD connector
    [MainBoard.sch]
2021-03-27 renamed connector
    [MainBoard.sch]
2021-03-28 removed erroneus R on I2c
    [HVSide.sch]
2021-03-28 ported prominent of newcar as optional
    [HVSide.sch]
2021-03-28 Using standard LM1117 regulator
    [MainBoard.sch]
2021-03-28 added page settings title etc...
    [HVSide.sch, MainBoard.sch, MainShutdown.sch]
2021-03-28 finished footprint association
    [HVSide.sch, MainBoard.sch, MainShutdown.sch]
2021-03-30 Done early board
    [HVSide.sch, MainBoard.kicad_pcb, MainBoard.sch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]
2021-04-30 board soldered
    [HVSide.sch, MainBoard.kicad_pcb, MainBoard.sch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]
2021-05-03 added printout of the schematic V3
2021-05-13 corrected pulldown and air+ mosfet driving
    [MainBoard.sch, MainShutdown.sch]
